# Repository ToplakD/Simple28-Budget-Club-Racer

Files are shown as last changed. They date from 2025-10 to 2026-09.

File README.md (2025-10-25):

# Simple28-Budget-Club-Racer
ALZA-Racing Simple28 is a Free to 3D print low-cost model concept, where almost all components of the car can be 3D-printed by the user using PLA filament.

The car is designed around low speed 030 micro motor, which should not exceed 14,000 RPM at the rated 5V, or 20,000 RPM at 7.4V.

Its simple design and low weight allow for good agility of the model through corners and during acceleration.

The model is not intended for professional racing or aggressive driving, but for enjoying with friends and requiring minimal maintenance with little investment. "Smooth is Fast."

# Where to download complete set of files:
https://cults3d.com/en/3d-model/game/simple-28-budget-club-racer-1-28-rc-car

# Basic Video Assembly instruction:
https://www.youtube.com/watch?v=FzzgdqYHlRI

# Video of beta version here (track 10x6 meters)
https://www.youtube.com/watch?v=D2kx7N0QyHI

# Updates will be posted in our FB Group:
https://www.facebook.com/groups/simple28rc

# What else you need for completing the build:
    Pinion Gear module 0.5 8-10 teeth for 1.5 shaft diameter (can be used from Slot cars)
    Spur Gear module 0.5 40t (can be used from Slot cars)
    Solid axle 3mm x 70mm
    M2 hardware
    Brushed motor in 030 size 13 - 14.000 RPM rated on 5v
    1/28 rear tires 14mm wide
    1/28 front tires 8.5 - 9.5mm
    Brushed ESC for 2s LiPo with at least 4A
    Servo motor 4.3 - 6g
    Screwdriver TX6
    Screwdriver 0.9mm Hex
    Lexan body 98mm wheelbase
    Bearings with flange 3x7x3 - 6pcs
    Radio and Receiver
    LiPo battery, 2s 200-350mAh

Please note that H-Plate needs to be updated or printed in harder material than PLA due to its left to right flex, affecting the car direction.

# Best experience with use of Optional Carbon Fiber:
https://shop.alza-racing.com/en/29-simple28

# 3D printing settings

Parts should be printed with 0.2mm layer height. PLA is the material of choice, minimum 3 walls, chassis and flat parts with 100% infill.

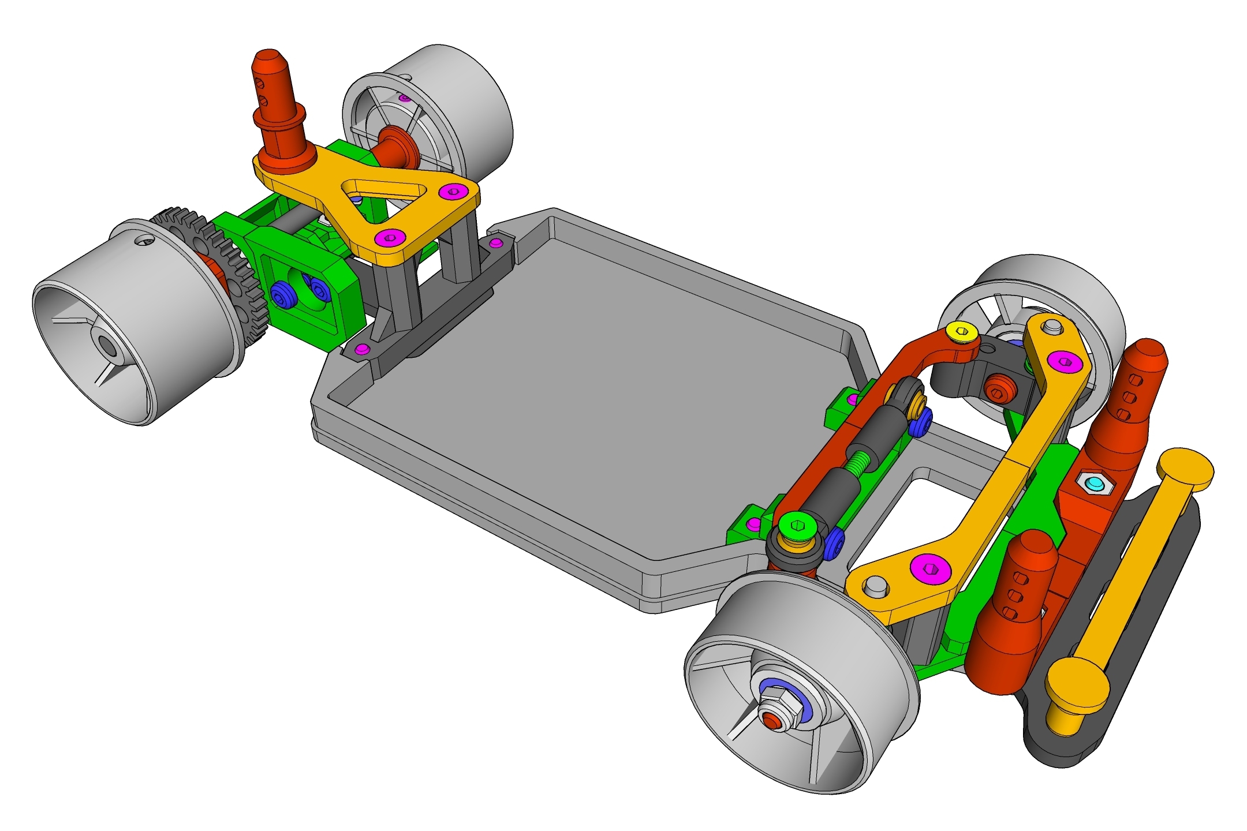
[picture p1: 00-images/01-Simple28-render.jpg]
Simple28 Render


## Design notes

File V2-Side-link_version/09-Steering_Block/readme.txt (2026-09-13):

Steering block - 2 versions
M2 and M2.5 is related to front screw for holding the kingpin

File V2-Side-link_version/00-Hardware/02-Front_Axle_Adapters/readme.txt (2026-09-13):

Numbers 290-310 are related to outer hole diameter, print all to see on which one bearings fit the best.

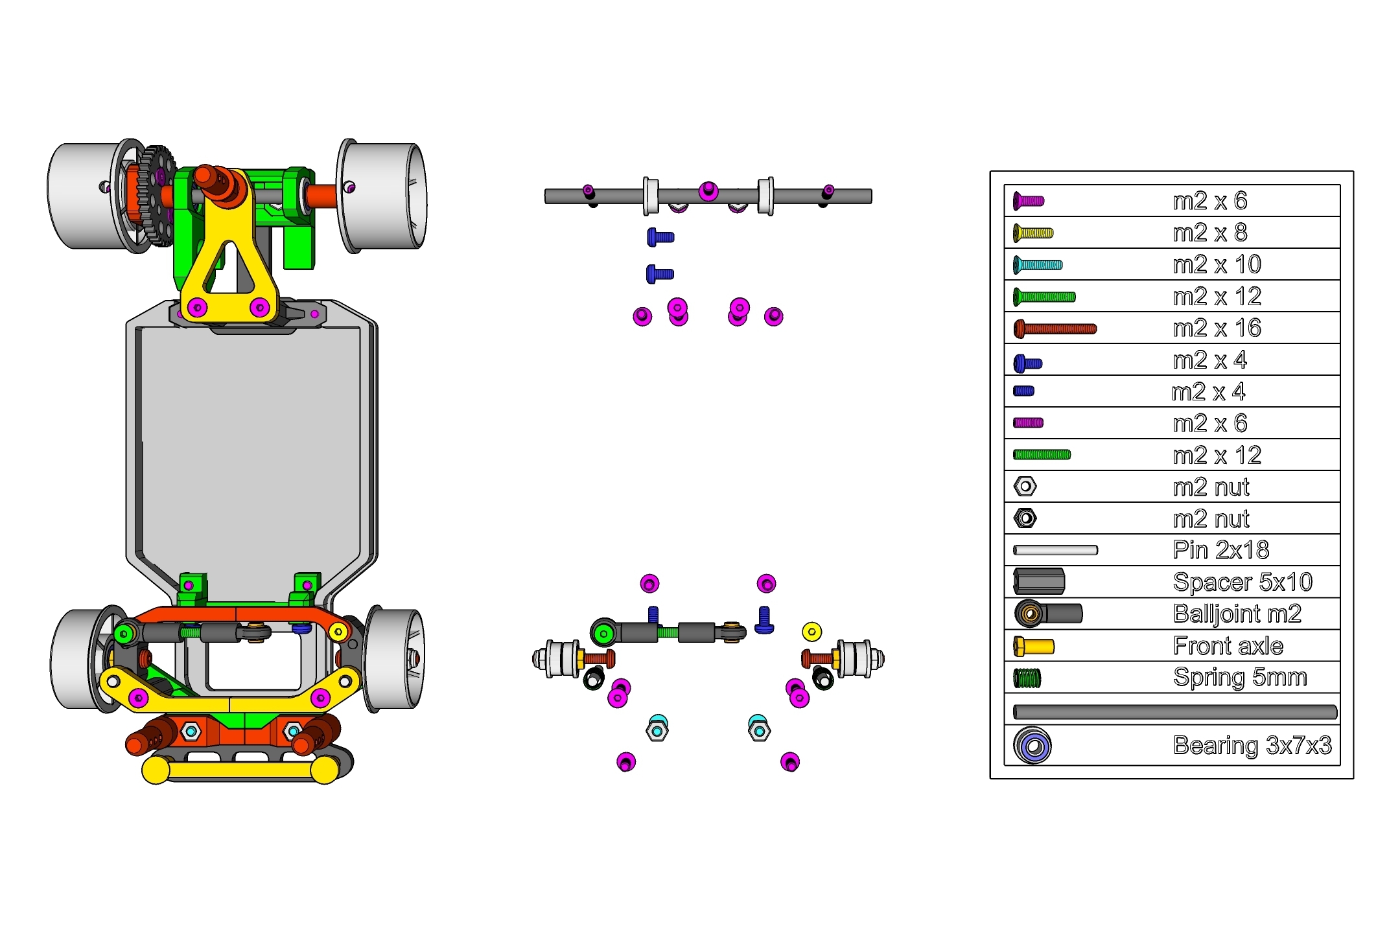
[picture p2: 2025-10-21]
V1-H-Bar_version/00-images/03-Hardware_list.jpg

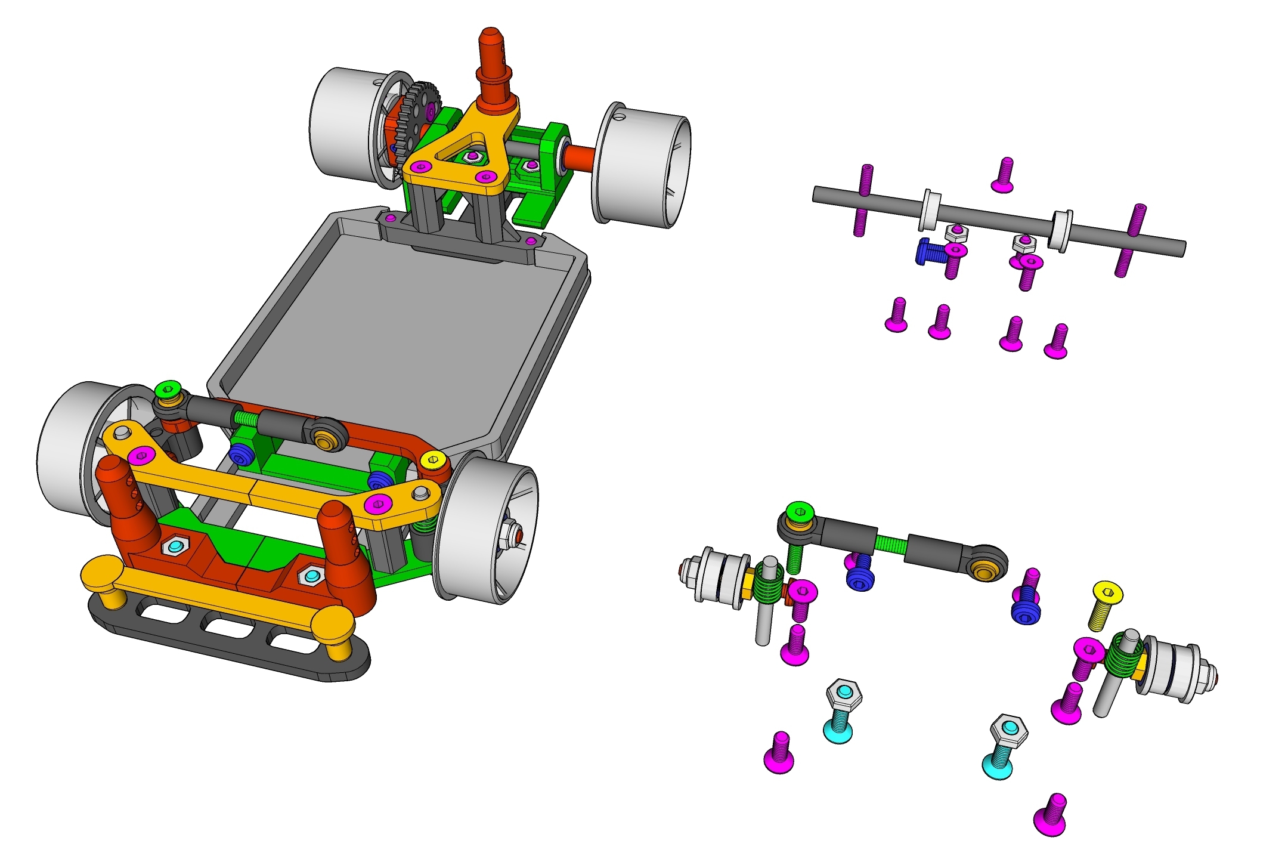
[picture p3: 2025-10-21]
V1-H-Bar_version/00-images/02-Hardware_view.jpg

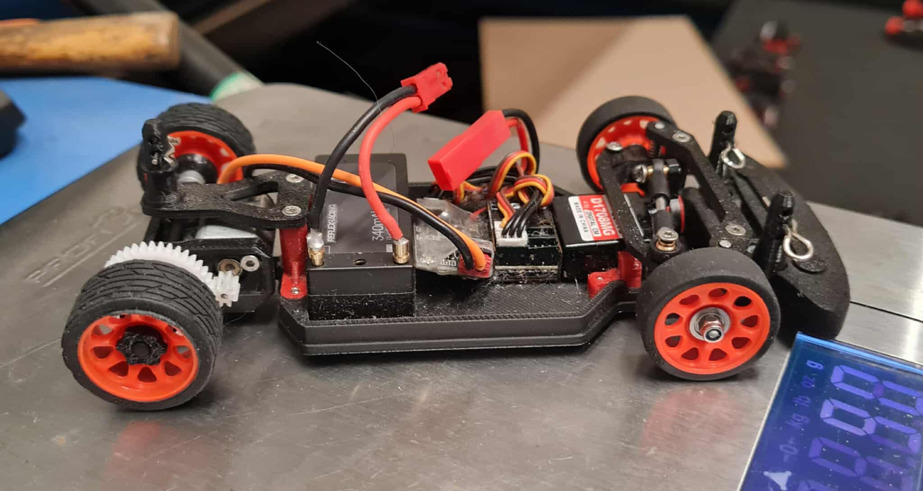
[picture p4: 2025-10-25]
V1-H-Bar_version/14-Stock_wheel_adapters/rear-wheel-mounted.jpg

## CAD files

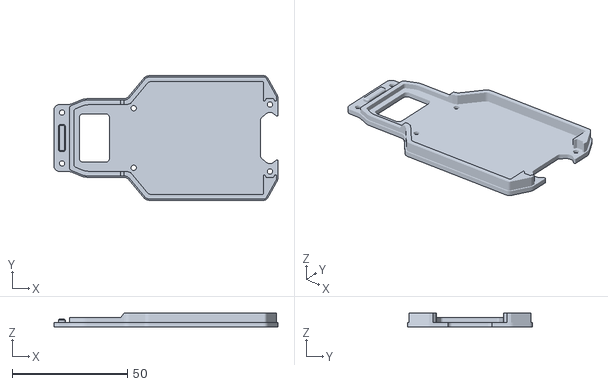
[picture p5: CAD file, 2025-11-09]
V1-H-Bar_version/01-Chassis/01-Chassis.stl
97.0 x 54.0 x 6.00

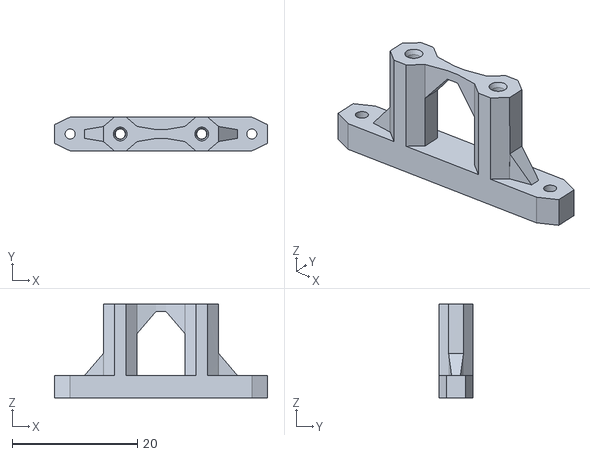
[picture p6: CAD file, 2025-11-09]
V1-H-Bar_version/02-H_Holder/02_02-H_Holder.stl
34.0 x 5.40 x 15.0

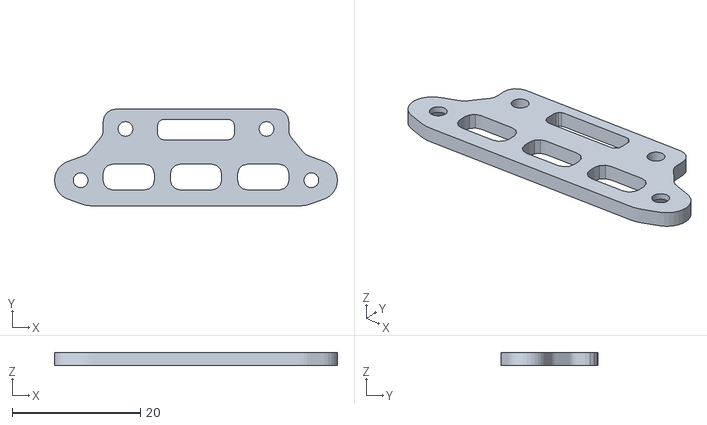
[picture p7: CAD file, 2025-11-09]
V1-H-Bar_version/03-Bumper_Holder/03_01-Bumper_Holder-Bottom.stl
44.1 x 15.1 x 2.00

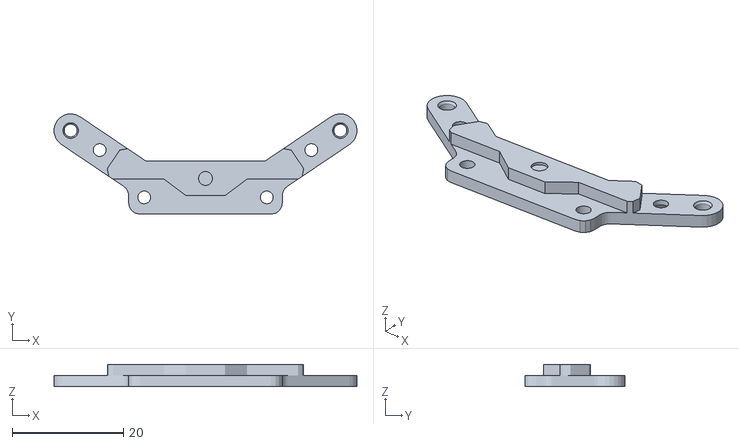
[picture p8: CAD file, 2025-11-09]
V1-H-Bar_version/04-Lower_arm/04_02-Lower_arm-normal.stl
54.4 x 18.0 x 4.00

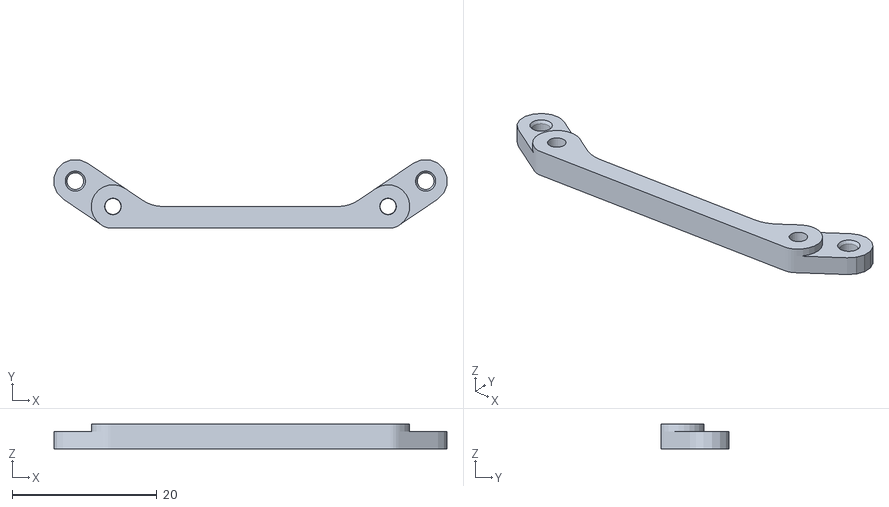
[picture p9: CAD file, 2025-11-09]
V1-H-Bar_version/05-Upper_Arm/05_01-Upper_Arm-HIGH-normal.stl
54.3 x 9.44 x 3.40

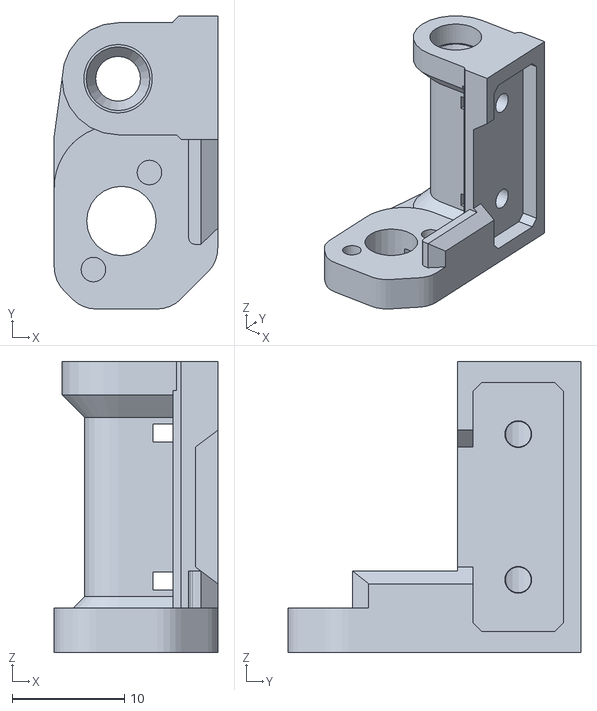
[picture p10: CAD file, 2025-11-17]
V1-H-Bar_version/06-Motor_mounts/6mm-bearings/06-Motor_Mount-6mm-40-10.stl
14.6 x 26.1 x 26.0

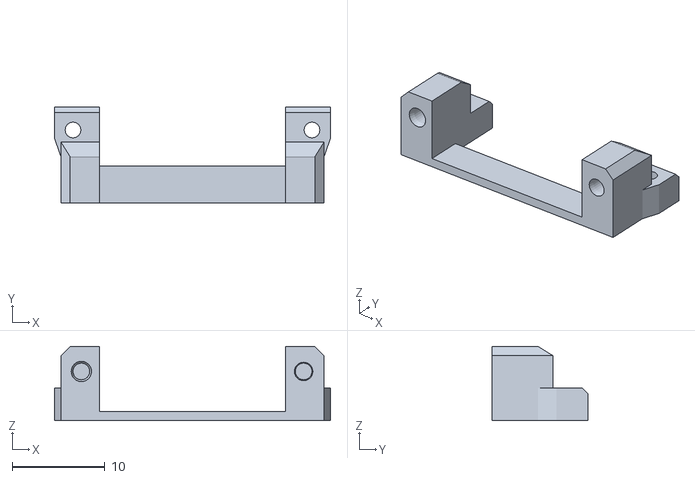
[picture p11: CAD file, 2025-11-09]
V1-H-Bar_version/07-Servo_Holder/07_01-Servo_holder-Standard.stl
29.8 x 10.4 x 8.00

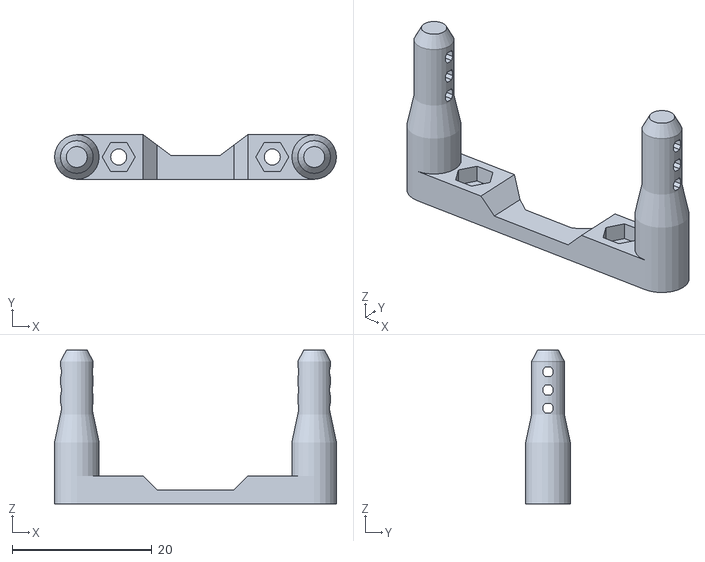
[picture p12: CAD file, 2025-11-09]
V1-H-Bar_version/08-Body_Post/08_02-Body_Post_Front-Combined-2mm.stl
40.4 x 6.40 x 22.0

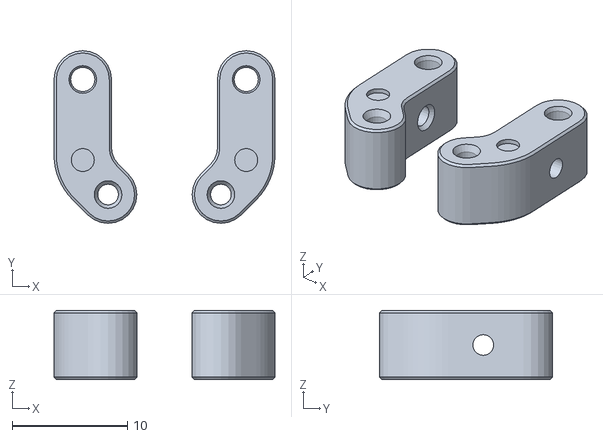
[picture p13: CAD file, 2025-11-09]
V1-H-Bar_version/09-Steering_block/09-Steering_Block-M2.stl
19.2 x 15.0 x 6.00

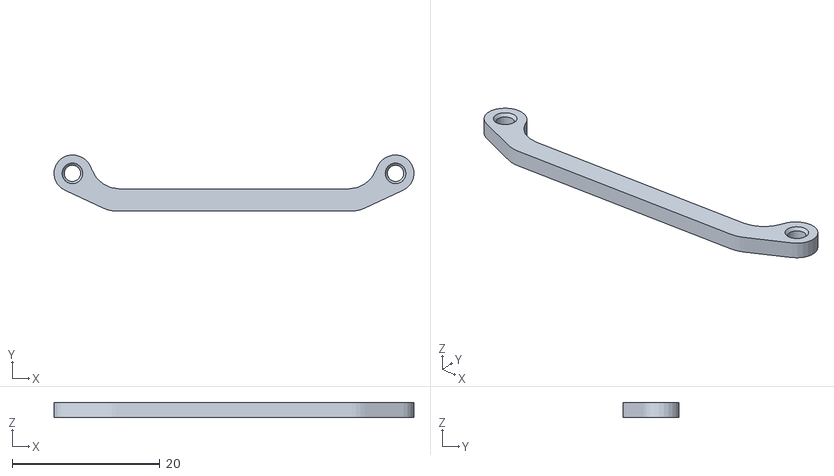
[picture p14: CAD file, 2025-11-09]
V1-H-Bar_version/10-Steering_Connection/10_01-Steering_Connection-Toe_out-1deg.stl
48.7 x 7.59 x 2.00

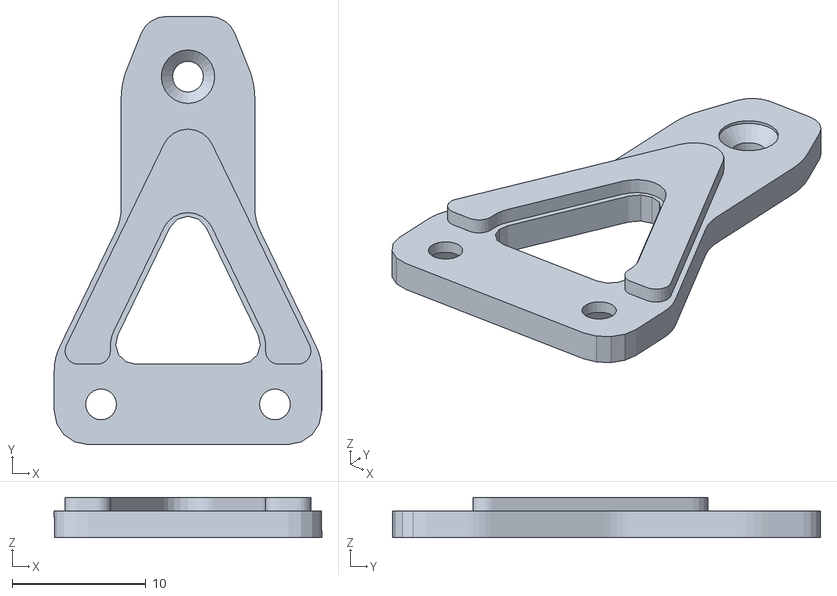
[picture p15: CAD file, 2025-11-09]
V1-H-Bar_version/11-Body_Post-Holder-Rear/11-Body_Post_Holder_Rear.stl
20.0 x 32.0 x 3.00

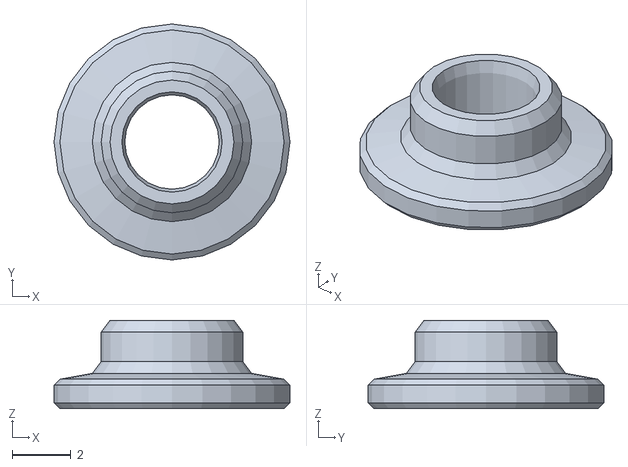
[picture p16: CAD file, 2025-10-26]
V1-H-Bar_version/12-Rear_axle_spacers/12_rear_axle_spacer-3mm.stl
8.00 x 8.00 x 3.00

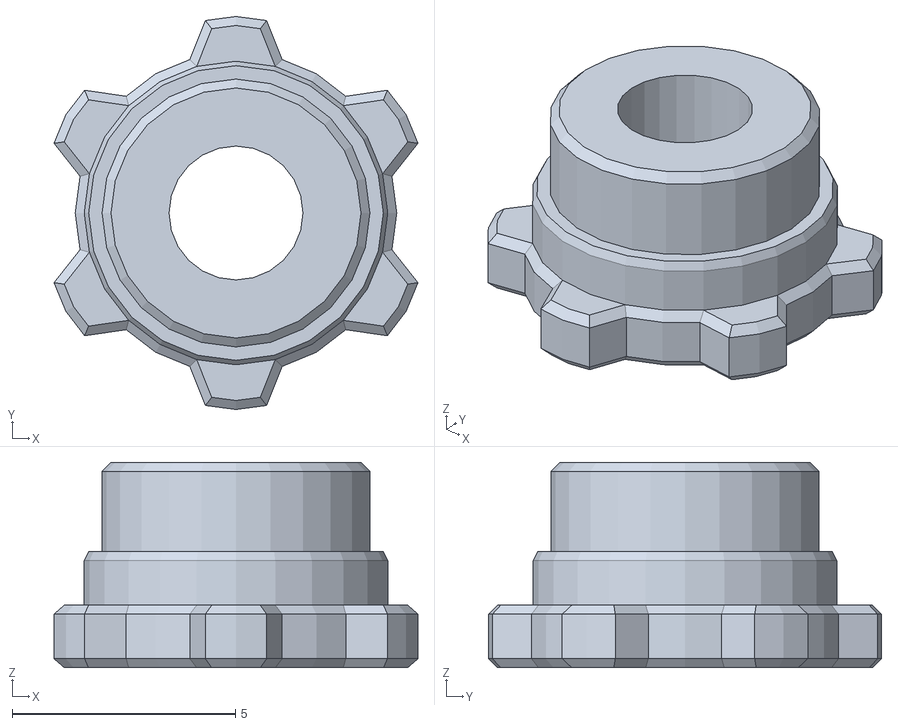
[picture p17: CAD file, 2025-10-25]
V1-H-Bar_version/14-Stock_wheel_adapters/02-Wheel-Holder.stl
8.15 x 8.80 x 4.60

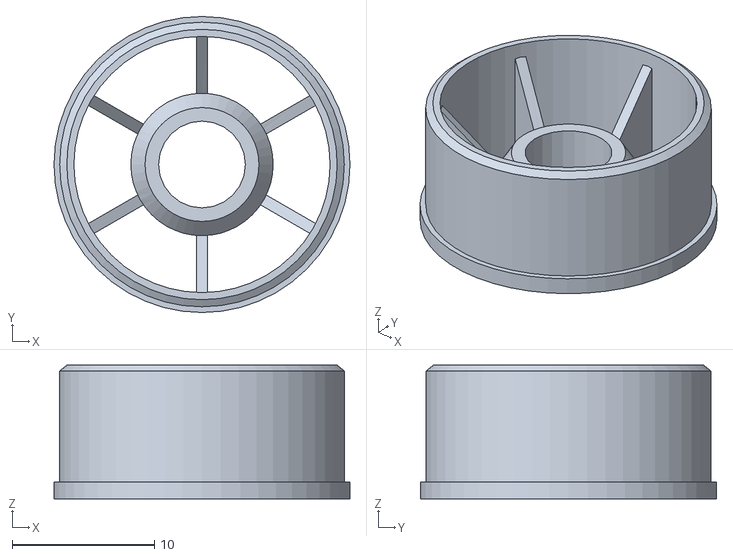
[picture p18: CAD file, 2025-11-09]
V1-H-Bar_version/15-Rims/Front-8.5mm/20mm/6mm-bearing/11-Rims_Front-20-605.stl
20.8 x 20.8 x 9.40

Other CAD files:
V1-H-Bar_version/06-Motor_mounts/7mm-bearings-Flanged/06-Motor_Mount-7mm-40-08.stl
V1-H-Bar_version/15-Rims/Front-8.5mm/20mm/7mm-bearing/11-Rims_Front-20-705.stl
V1-H-Bar_version/15-Rims/Front-8.5mm/21mm/6mm-bearing/11-Rims_Front-21-605.stl
V1-H-Bar_version/15-Rims/Front-8.5mm/21mm/7mm-bearing/11-Rims_Front-21-705.stl
V1-H-Bar_version/01-Chassis/01-Chassis-no-TAB.stl
V1-H-Bar_version/02-H_Holder/02_01-H_plate-7mm.stl
V1-H-Bar_version/04-Lower_arm/04_01-Lower_arm-tight.stl
V1-H-Bar_version/05-Upper_Arm/05_00-Upper_Arm_10mm_Spacer.stl
V1-H-Bar_version/05-Upper_Arm/05_01-Upper_Arm-HIGH-tight.stl
V1-H-Bar_version/05-Upper_Arm/05_01-Upper_Arm-LOW-normal.stl
V1-H-Bar_version/05-Upper_Arm/05_01-Upper_Arm-LOW-tight.stl
V1-H-Bar_version/06-Motor_mounts/6mm-bearings/06-Motor_Mount-6mm-40-08.stl
V1-H-Bar_version/06-Motor_mounts/6mm-bearings/06-Motor_Mount-6mm-40-09.stl
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

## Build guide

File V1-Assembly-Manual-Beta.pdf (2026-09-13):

# Budget Club Racer

# SIMPLE28

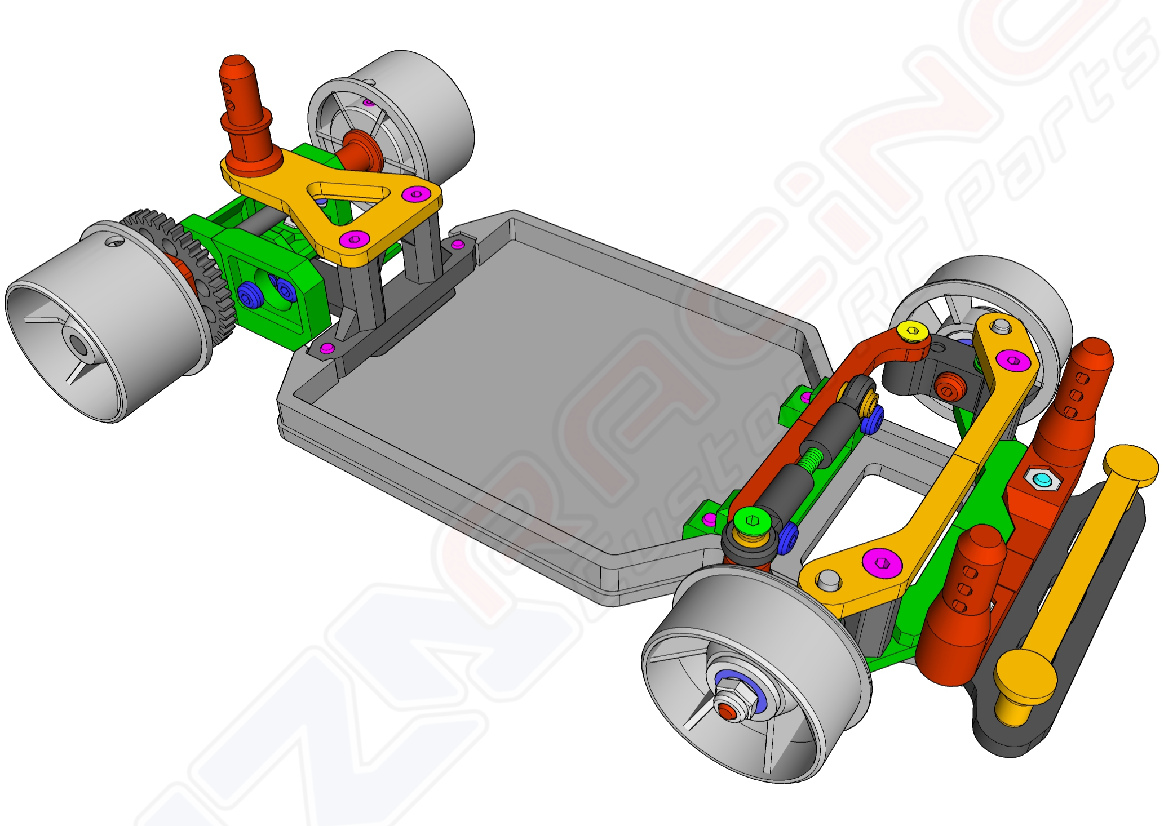
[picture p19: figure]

### Simple28 is a Free to 3D print lowcost model concept, where almost all components of

the car can be 3D-printed by the user using PLA filament.

### The car is designed around low speed 030 micro motor, which should not exceed 14,000

RPM at the rated 5V, or 20,000 RPM at 7.4V.

### Its simple design and low weight allow for good agility of the model through corners and

during acceleration.

### The model is not intended for professional racing or aggressive driving, but for enjoying with friends and requiring minimal maintenance with little investment. "Smooth is Fast."

### 3D printing settings:

Parts should be printed with 0.2mm layer height.
PLA is the material of choice, minimum 3 walls, chassis and flat parts with 100% infill.

### Where to download? https://cults3d.com/en/3dmodel/game/simple-28-budgetclubracer-1-28-rccar

### What licence applies to Free Simple28? Model is released under CULTS Private Use

### You are authorized to:

Print and use the 3D prints of the 3D model for private use, in unlimited quantity.

### Share the images of your 3D prints of the 3D model on communication media such as

social networks or websites.

### What is not allowed: No commercial use or public sharing of the 3D model; No modification or adaptation of the 3D model for public sharing or sale;

No distribution, sale, donation or exchange of the digital files of the 3D model.

### For updates follow Facebook Group: https://www.facebook.com/groups/simple28rc

### Optional parts available on Alza-Racing Website https://shop.alzaracing.com/

### Do I need to buy anything from mentioned website?

No, you don't. Car is available as free to print version, so you just download the files for personal use, source the hardware and you are ready to print, assemble and drive.

### Other informations:

The model is not sold as an assembled kit, it is not a toy, and as such it is not intended for persons under 18 years of age.

To complete the assembly of the model, the structural parts must be 3D-printed.

Building the model requires good eyesight, patience and a steady hand.

### If you’ve never managed to complete a puzzle of 100 or more pieces, then this model may

not be suitable for you.

# Simple28 Budget Club Racer 1/28 scale

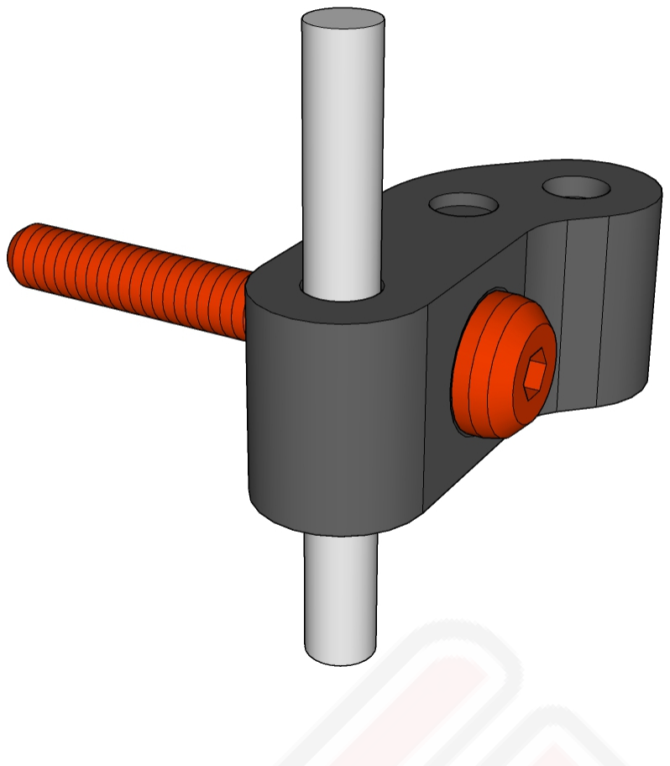
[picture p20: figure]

01 Steering block assembly:
Screw M2x16 Button head screw into steering block as shown on picture. Assemble left and right piece mirrored.
Push the 2x18mm PIN into steering block (it should stick out 5mm on bottom side, 7mm on top side). At this time you can also prethread rear hole which will later be used for fastening steering connection.

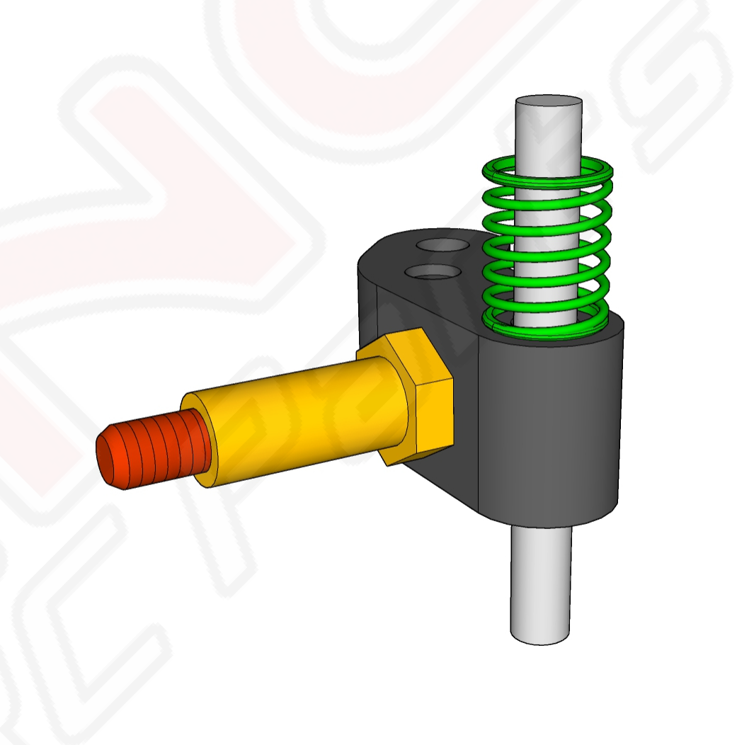
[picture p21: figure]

02- Steering block bearing holders:
Now it's also time to add bearing seat (front axle) onto M2 screw, so your bearings will sit propperly. You can use 3d printed part, source axles from other brands, or check ALZA optional parts.

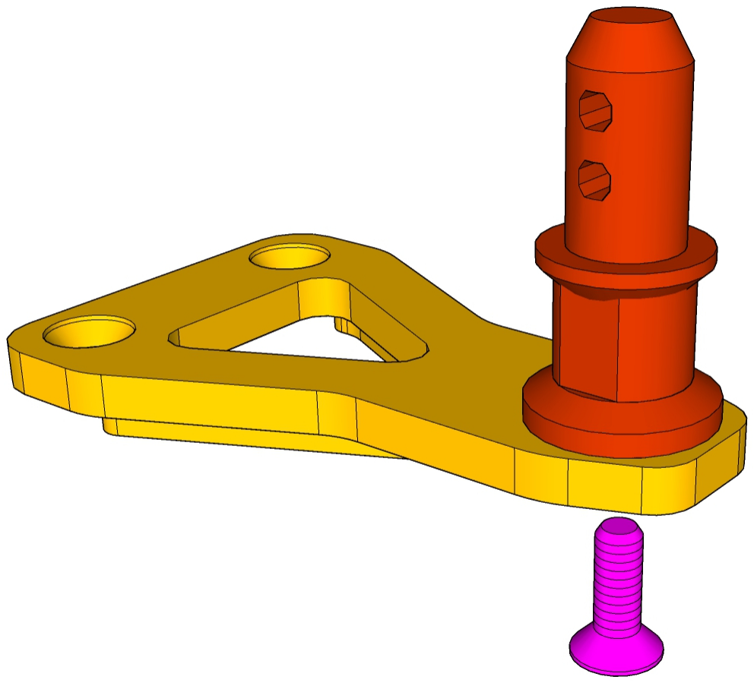
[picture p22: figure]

03 Rear body post holder assembly:
You will need M2x6 Countersunk screw, 3d printed Rear body post and Rear body post holder. Assemble it like on picture.

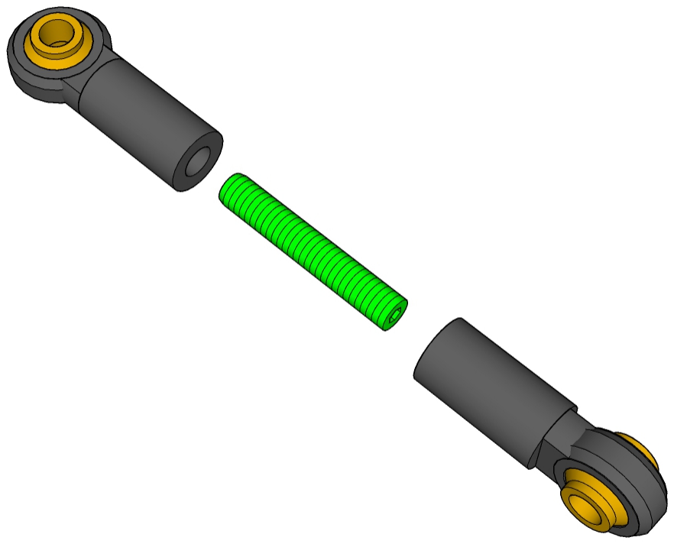
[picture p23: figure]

05 Servo steering link assemlby:
Take 2 14mm long ball joints and 1 m2 x 12 grub screw. Screw the grub into 1st ball joint about 3mm deep and take out the screw. Than screw same screw into 2nd ball joint also about 3mm deep. Now you can fasten both onto the screw, leaving about 6mm gap between ball joints. Half turn of one ball joint coresponds to 0.2mm change in length.

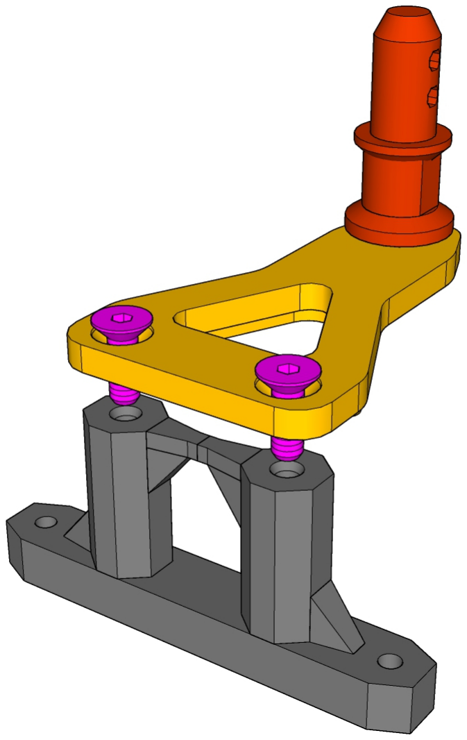
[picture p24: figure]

04- Rear H-Holder prepare and assembly:
Take your H-Holder and prethread all 6 screw holes. Once you succeded, than you can take rear body post holder plate and screw it onto H-Holder with 2pcs M2x6 countersunk screws.

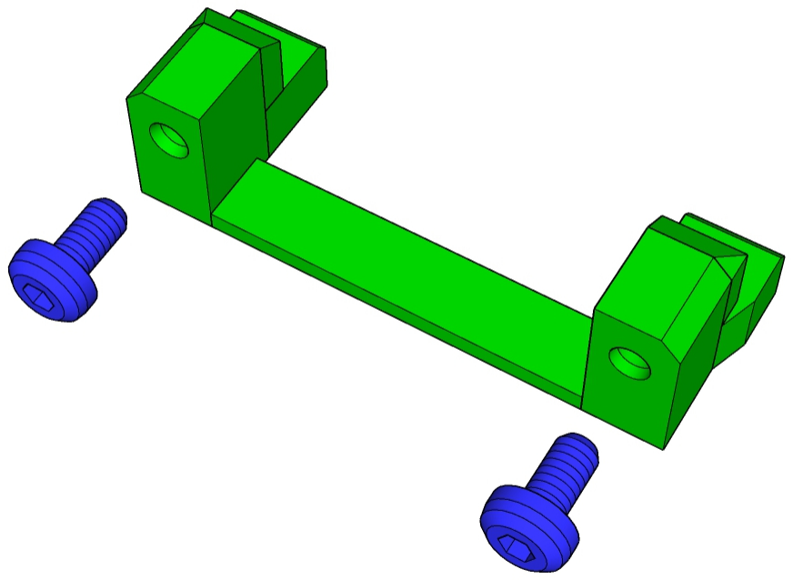
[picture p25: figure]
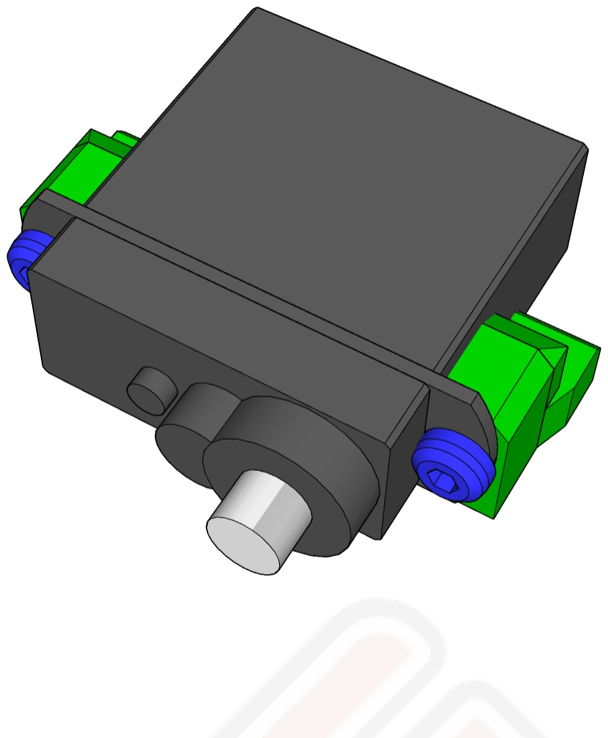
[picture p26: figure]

06 Servo mount prepare:
Take your printed servo mount and prethread all four holes for at least 5-6 turns. For fastening the servo, you will need 2pcs M2x4 Buttonhead Screws. Than you can put in your servo and tighten it gently so that it sits in place. No brute force needed here.

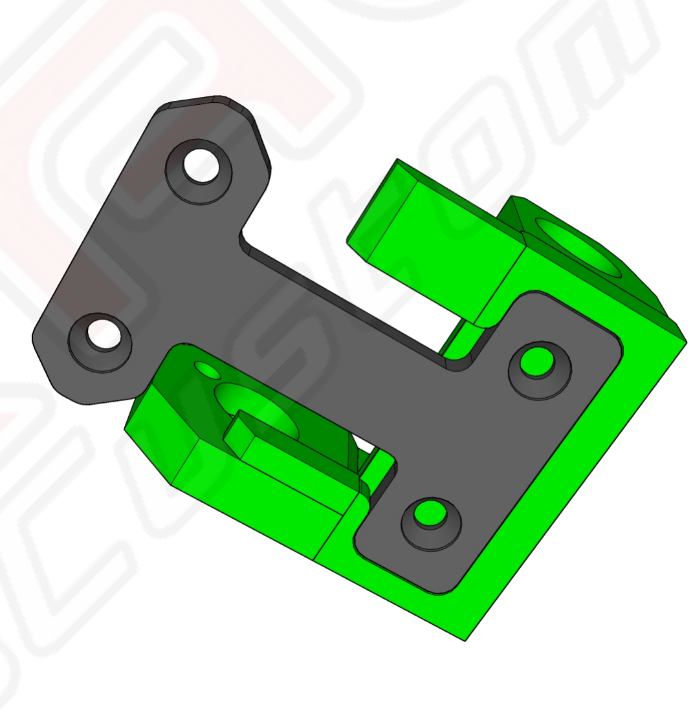
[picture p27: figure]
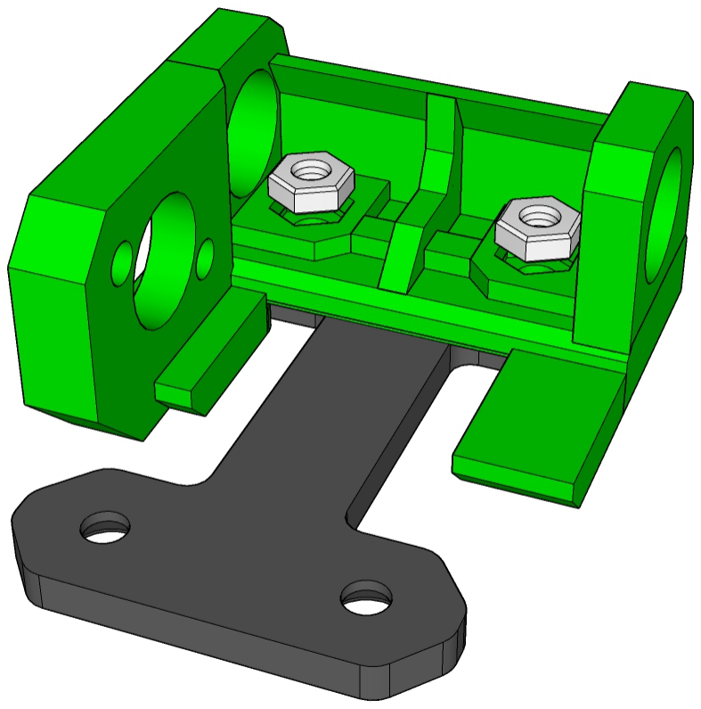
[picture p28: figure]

08 Motormount and preparation:
Put H-Plate into motormount and puncture those two holes at the bottom of motormount. Turn it arround and press in 2pcs M2x6 regular nuts.

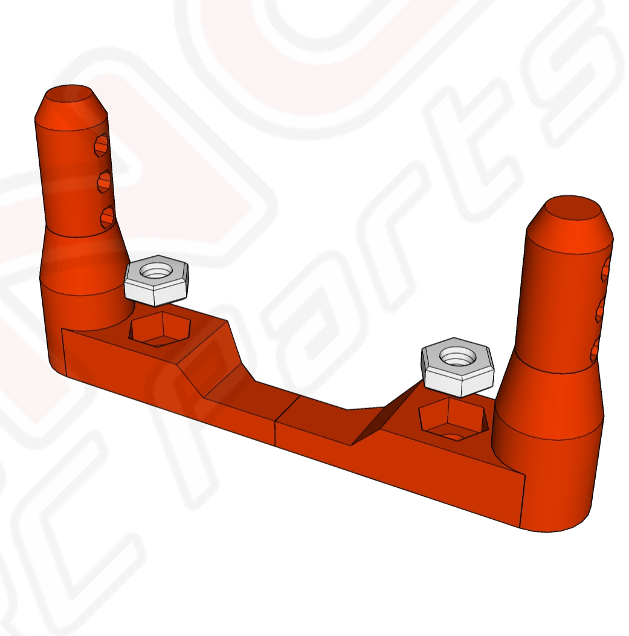
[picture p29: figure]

07 Front body post holder assembly:
Take 2 regular M2 Nuts and press them into front body post.
It's not that hard that it would need it's place in the manual. But some will appreciate having most steps of assembly covered.

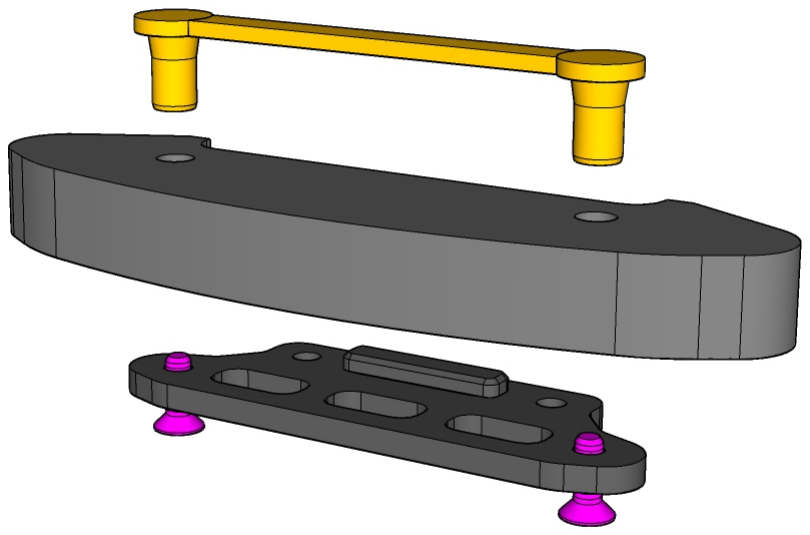
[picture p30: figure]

10 Front Bumper assembly:

Put 2x M2x6 screws into the Bumper holder, place the bumper (bought or DIY) onto those 2 screws. Than add Bumper Top holder part (either single or One-piece like on picture) into the Foam Bumper. Gently screw the screws until you can not move the top part which is holding the foam bumper. Foam bumper is not needed, but its helpful when crashing. You can either made it DIY or get one on ALZA webpage.

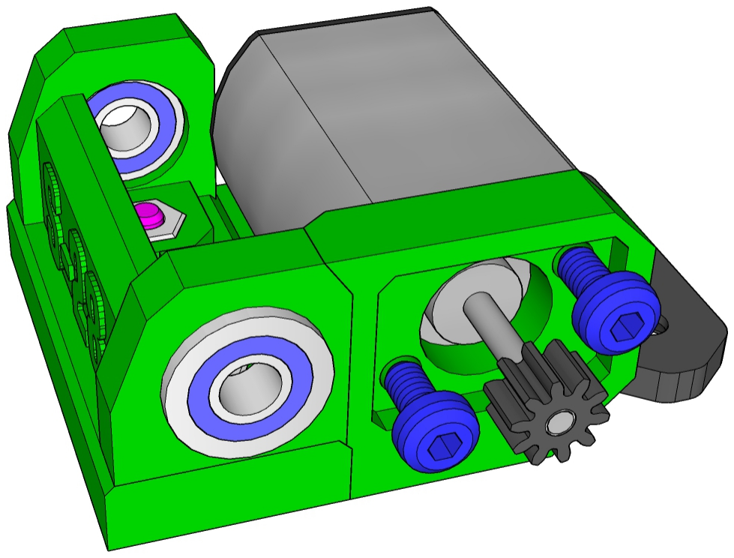
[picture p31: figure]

09 Finalizing Motormount assembly:
Take 2x M2x6 Countersunk screws and screw H-Plate onto motormount. Press in the bearings, add 030 motor and fasten the motor with use of 2x M2x4 Buttonhead Screws.

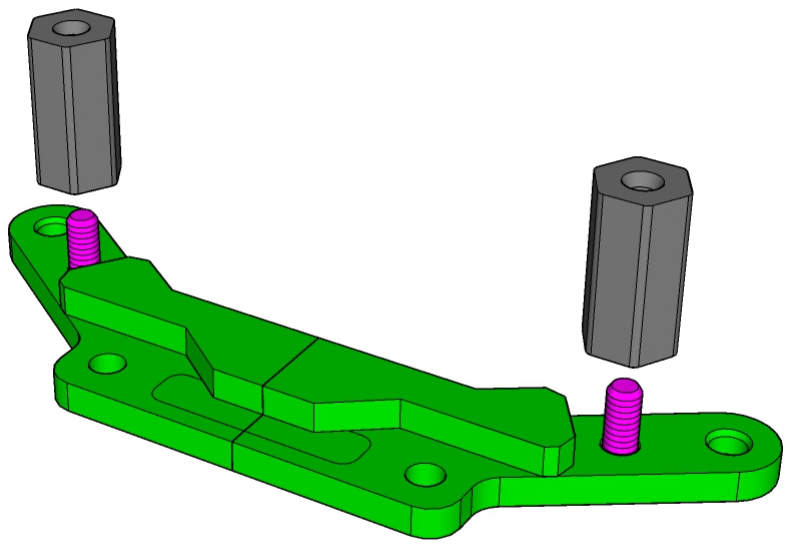
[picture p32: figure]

11 Front lower arm preparation:
Firtst take 2 M2x6 screws and 10mm distance spacers and fasten them onto lower arm. Once you have succeded, you can put assembled steering blocks onto the lower arm. The Holes for pins will need some preparation, as Pin should slide freely through the hole.

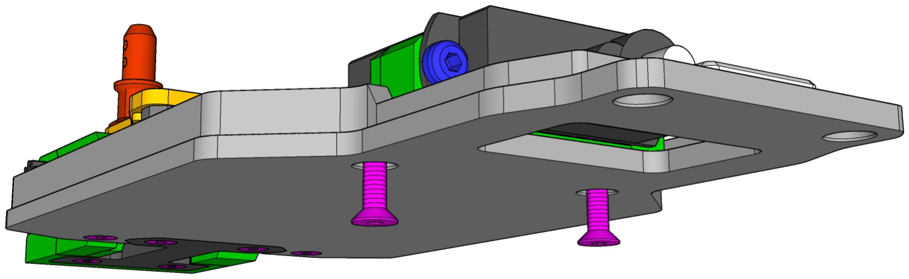
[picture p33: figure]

14 Adding servo to chassis:
Take 2x M2x6 Countersunk screws and screw completed servo assembly onto chassis plate.

12 Front final assembly:
Remove springs, put your upper arm in place and fasten it with 2x M2x6 Countersunk screws. Check if motion of steering block is free, if not adjust the holes on arms. Once you get smooth motion, take down the upper arm, install pins, and put upper arm back.

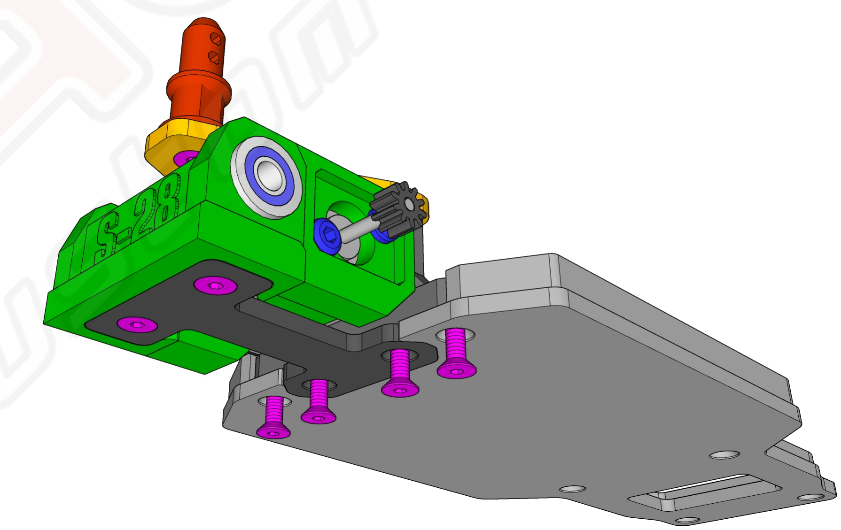
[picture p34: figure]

13 Assemble Back and chassis:
Take 4x M2x6 screws, put chassis and rear together and fasten the screws. Simple.

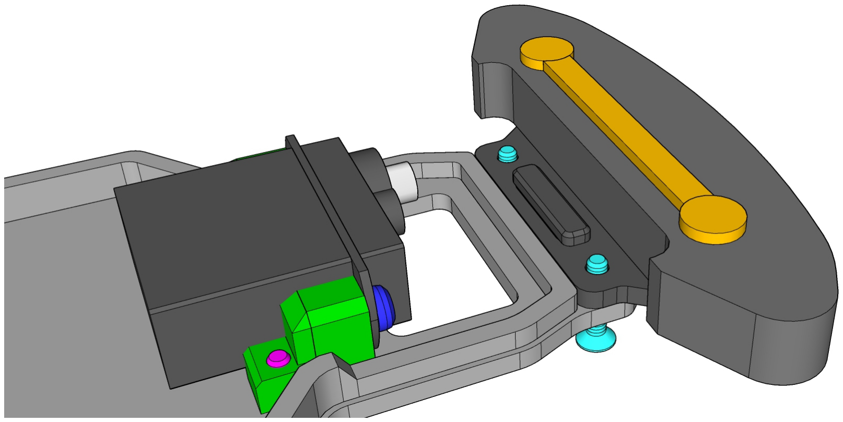
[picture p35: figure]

15 Adding Bumper to chassis:
Take 2x M2x10 Countersunk screws and put them through chassis and bumper holder.

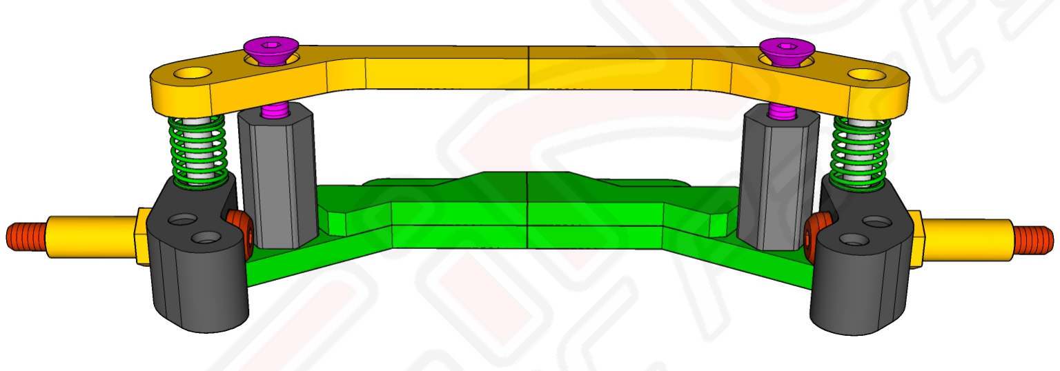
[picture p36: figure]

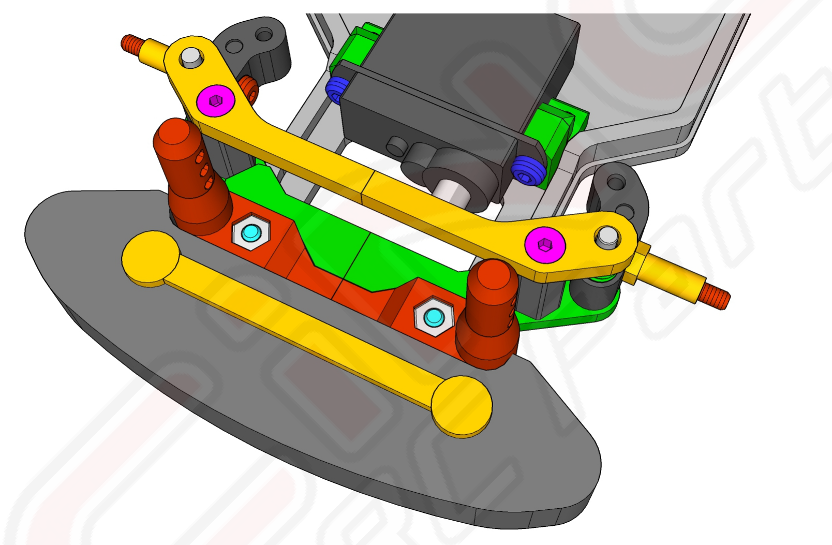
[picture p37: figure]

17 Adding Front Body post to assembly: Add Body posto over the lower arm and fasten those two screws which are holding together whole frontend.

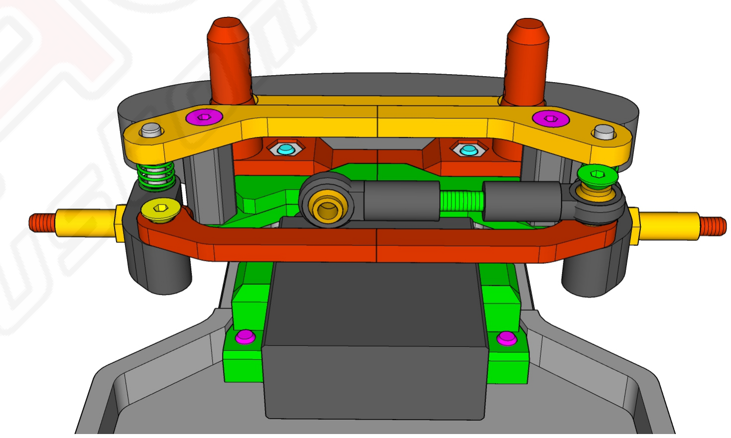
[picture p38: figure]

18 Connect Steering blocks together:
Put steering connection onto steering blocks. Fasten left side with M2x8mm Countersunk and right side with M2x12mm countersunk screw. Allow little play on steering connection, adjust the hole if needed. Check steering blocks movement in all directions.

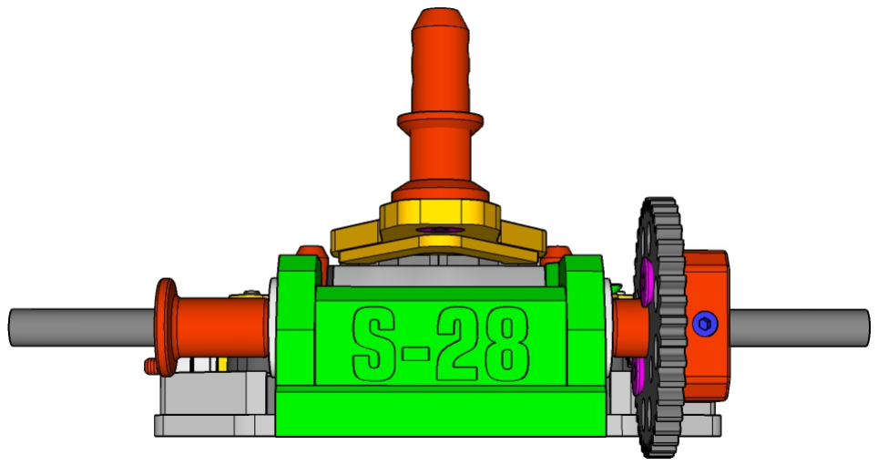
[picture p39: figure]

19 Insert rear axle:
Install 70mm long axle into motormount. Add 40t spur gear (you can use Module 0.5 Slot car spur). Ajust spur gear position so the axle distance is same on both sides. Add some spacers left and right and you are ready to attach rear rims.

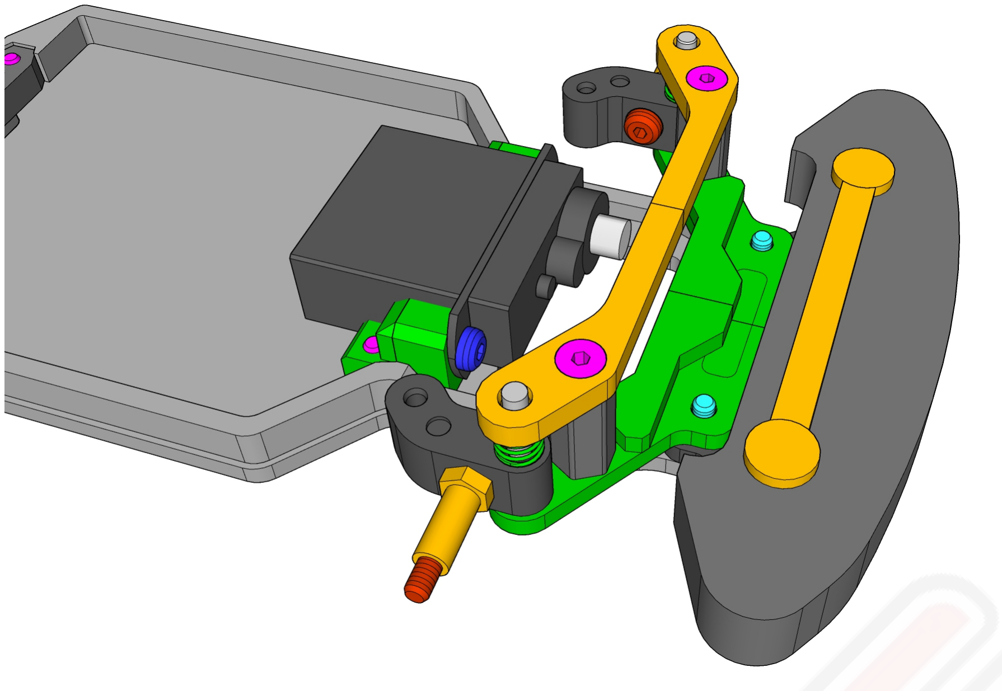
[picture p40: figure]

16 Adding complete Front end to chassis: Take completed front end and put it over bumper which you installed earlier. Check if the tabs on bumper and lower arms are clean and they sit well together without angle to any side.

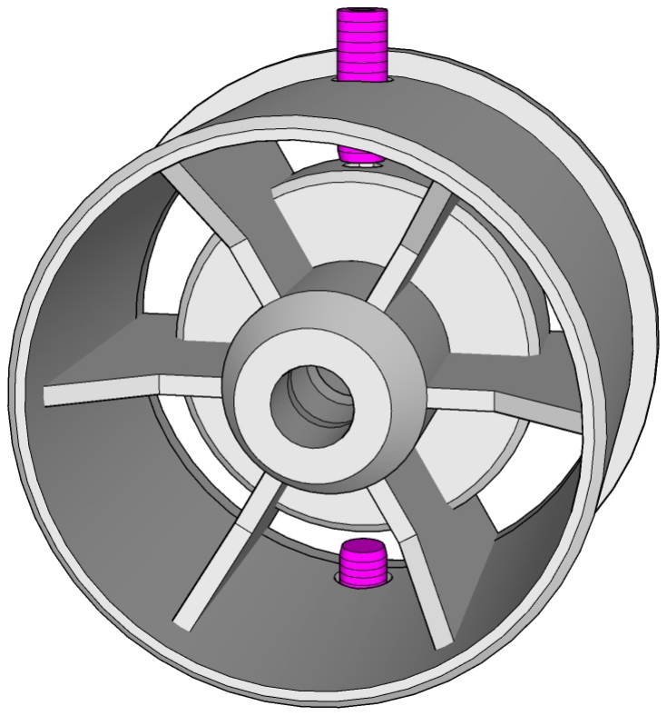
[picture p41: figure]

20 Rear rims preparation:
Take M2x6 grub screw. Screw it from the side into the rim, only 5-6 turns and take it out. Repeat same step on opposite side of the rim. Than take longer screw and thread the complete hole to the middle of the rim. If you will try threading with grub, there is a high chance that you will ruin it's head. Once threaded, clean the middle hole and screw both grub screws into place.

M2 x 6 | 17 x Countersunk
M2 x 8 | 1 x Countersunk
M2 x 10 | 2 x Countersunk
M2 x 12 | 1 x Countersunk
M2 x 12 | 2 x Buttonhead
M2 x 4 | 4 x Buttonhead
M2 x 4 | 2 x Grub Screw
M2 x 6 | 4 x Grub Screw
M2 x 12 | 1 x Grub Screw
M2 nut | 4 x Regular Nut
M2 nut | 2 x Locking Nut
2x18 pin | 2 x Dovel Pin
M2 x 10 | 2 x Standoff
M2 x 14 | 2 x Ball joint
M2 x 8 | 2 x Front Axle
5mm | 2 x Spring
70mm | 1 x Solid Axle
3x7x3 | 6 x FL Bearings

## What hardware is needed to complete the build?

Below is the complete list of hardware that is needed to complete one Simple 28. Some parts are optional in the list but can also be printed. (Standoff and Front Axle).

## Where can I buy needed hardware?

Screws and nuts and pins can be bought in local hardware stores or online.
Axles can be used from 1/24 Slot cars, ball joints are available at local hobby shops, same

### with bearings. Springs you can salvage from your used ballpoint pen :)

## What type of spur and pinion gear is needed?

Current motormount alows total of 48t. So 40t Spur gear + 8t Pinion.

### Spur gear with 3mm bore and Piniont with 1,5mm bore. Both are available in Slotcar

shops worldwide.

Motormount which allows 49 and 50t total gearing will be available soon.

## Optional, can be 3D printed

## Optional, can be 3D printed

## Optional for DIY spur gear

## 030 Brushed motor:

Since this is low budget low weight car, it does not need or like powerfull motor.

### The car is designed around low speed 030 micro motor, which should not exceed 14,000

RPM at the rated 5V, or 20,000 RPM at 7.4V.

### PPN7PA12C1 Motor from Minebea / NMB Technologies is suggested, or something with

similar RPM at rated voltages. Search online for Datasheet of the motor.

### Also search for PPN7PA11C on bigger online marketplaces :)

### Motors from currently available 1/24 buggies are not suggested, as power and RPM are

too high for this low weight car.

If you go with high rpm motors, you should consider using 1s ESC and different gear ratio.

## Servo motor:

Car is designed arround regular 4.3g servos which are widely available.
Any that fit's your budget will do.

## Suggested ESC:

### Any 2s ESC with reverse and brake function that fits your budget. On bigger online marketplaces you can get them from 5 € / $ to very high priced options. Low budget

options are always recommended and most of them work very well for the price.

## Lipo Battery:

### Use 2s Lipo with 200+ mAh. Car consumes about 100mAh if driven on carpet track for 10

minutes.

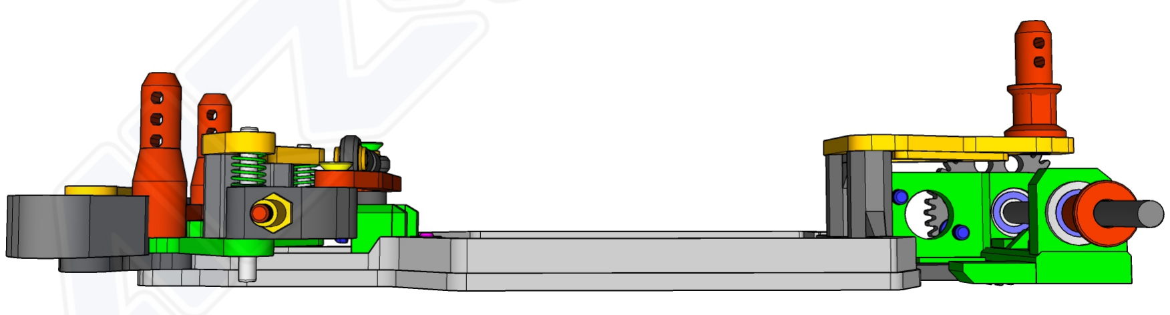
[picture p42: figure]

## For updates follow Facebook Group: https://www.facebook.com/groups/simple28rc

## Optional parts available on Alza-Racing Website https://shop.alzaracing.com/

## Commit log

2025-10-26 Added Rear Axle spacers
    [01-Wheel_hub.stl, 02-Wheel-Holder.stl, 06-Motor_Mount-6mm-40-08.stl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]
2025-10-26 Adding rims
    [11-Rims_Front-20-605.stl, 11-Rims_Front-20-705.stl, 11-Rims_Front-21-605.stl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]
2025-10-26 add rims
    [11-Rims_Rear-11x20-305.stl, 11-Rims_Rear-11x20-310.stl]
2025-10-26 update rims
    [11-Rims_Rear-11x20-300.stl, 11-Rims_Rear-11x20-310.stl]
2025-11-09 updating motor mounts
    [06-Motor_Mount-6mm-40-08.stl, 06-Motor_Mount-6mm-40-09.stl, 06-Motor_Mount-6mm-40-10.stl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]
2025-11-09 Updating Motormounts
    [06-Motor_Mount-6mm-40-08.stl, 06-Motor_Mount-6mm-40-09.stl, 06-Motor_Mount-6mm-40-10.stl]
2025-11-09 Update Front Rims
    [11-Rims_Front-20-605.stl, 11-Rims_Front-20-705.stl, 11-Rims_Front-21-605.stl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]
2025-11-09 Chassis Update
    [01-Chassis-no-TAB.stl, 01-Chassis-notab.stl]
2025-11-09 Update Chassis
    [01-Chassis-no-TAB.stl, 01-Chassis.stl]
2025-11-09 Update Parts
    [02_01-H_plate-7mm.skp, 02_02-H_Holder.skp, 03_01-Bumper_Holder-Bottom.stl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]
2025-11-09 Update Files
    [07_01-Servo_holder-Standard.stl, 08_01-Body_Post_Rear-0mm.stl, 08_01-Body_Post_Rear-1mm.stl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]
2025-11-09 Added Hardware
    [Hardware-Lipo.stl, Hardware-Motor-030.stl, Hardware-Pin-18x2.stl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]
2025-11-17 update motormounts
    [06-Motor_Mount-6mm-40-08.stl, 06-Motor_Mount-6mm-40-09.stl, 06-Motor_Mount-6mm-40-10.stl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]
2025-12-01 Added servosaver with 28t servo head
    [28T-Afrc-036.stl, 28T-Afrc-037.stl, 28T-Afrc-038.stl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]
2026-03-17 Upload Steering Axle
    [18-Steering_Axle-290.stl, 18-Steering_Axle-295.stl, 18-Steering_Axle-300.stl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]
2026-03-17 Upload parts
    [07-Servo_holder-Standard.stl, 09-Steering_Block-V2.stl, 10-Steering_Connection-452-Complete.stl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]
